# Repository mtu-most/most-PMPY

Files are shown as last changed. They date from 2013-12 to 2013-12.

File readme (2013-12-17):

MOST Push-Me-Pull-You 3D printer extruder drive

This design was developed as part of a project with the Michigan Tech Open Sustainability Technology Research Group http://www.appropedia.org/Category:MOST It is released under CC-BY-SA and was written primarily by Jerry Anzalone.

Printed Parts (count required):
motor end (1) (two different designs available) 
output_end_MkVII (1)
bearing_yoke_mk7 (1)
arm_mk7_inlet_pivot(1)
arm_mk7_inlet_spring(1)
idler_shaft (2)
input_half_4.62 (1)
output_half_4.62 (1)
Planet_4.62 (1)
Planet_4.62 (3)
carrier_MkVII_4.62 (1)

Non-printed parts (count):
M5 x 50mm hex-head cap screw (1)
M5 nut (1)
mk7 drive gear (1)
M3 x 8mm set screw (1)
M3 nut (4)
M4 x 16mm socket head cap screw (3)
M4 nylock nut (3)
M4 flat washer (9)
624zz bearing (3)
625 bearing (2)
M4 x 6mm aluminum standoff (2)
M4 nut (2)
4mm OD x 2mm ID teflon tubing of sufficient length for project
NEMA17 motor (1)
M3 x 12mm socket head cap screw (4)
M3 flat washer (8)
M3 x 45mm socket head cap screw (3)
M3 x 25mm socket head cap screw (1)
~25mm x ~10mm stiff compression spring (1)
608zz bearing (2)

Instructions
Clean up the sun gear. Press an M3 nut into the set screw nut trap and start the set screw. Do not tighten the screw into the motor shaft recess. Test fit the gear by pressing it onto the motor shaft and then removing it.
Clean up the motor end and attach to motor with M3 x 12mm screws each with an M3 washer.
Clean up the output end and press an M3 nut in the nut trap near the pointed screw boss.
Clean up the planetary carrier and press the M5 x 50mm screw through the central hole, seating the hex head in the recess provided. Press an M4 nylock nut into the nut traps.
Clean up the plantary gears, carefully removing support material and protrusions from threads, Press a 624zz bearing into each of the gears. Push a M4 x 16mm screw through the bearing and place 3 M4 flat washers on the screw below the bearing. Screw the gears onto the planteray carrier, tightening each and then loosing them up.
Work the sun gear in between the three planetary gears - insuring that the screws are very loose will facilitate this step.
With the sun gear seated in the center of the three planetary gears, tighten the planetary gear screws.
Work the planetary gears into the output half with the threaded portion of the M5 screw coming out opposite the annulus gear.
Work the input half onto the other side of the planetary gears making sure the pointed case screw boss lines up with same on the output half.
Line up the flat on the motor shaft with the set screw access port in the motor end then line up the set screw on the sun gear with the flat on the motor shaft. Press the transmission towards the motor so that the sun gear is pressed onto the motor shaft.
Apply white lithium grease to the planet gears and exposed portions of the annulus gears.
Put an M3 x 45mm screw with a washer into each of the three holes in the output end.
Place a 625 bearing on the M5 screw protruding from the planetary carrier. Feed the M5 screw through the output end and align the three M3 x 45mm case screws such that the pointed screw bosses are all lined up.
Place a washer and nut on each of the three case screws and carefully tighten the assembly.
Tighten the set screw in the sun gear through access port provided in motor case.
Clean up the arms and check that the 608zz bearings fit freely in their recesses.
Place a 608zz bearing in the recess and align its ID with the idler shaft hole in the arm. Start the idler shaft and carefully pound into place - they're tight by design.
Cut the 4mm OD x 2mm ID teflon tubing to the appropriate lengths. Cut two short (70-90mm) lengths for in-feed sides.
Prepare threads in both ends of the longer pieces of tubing (Bowden sheath). (Taper ends and screw M4 nuts onto them while a 2mm drill bit is inside the tubing to keep walls from collapsing. Work slowly and back the nut off on occasion. Thread ~12mm on one side and 6mm on the other. Ream the tubing with the 2mm drill bit. Pass a length of 1.75mm filament through the tubing to check for obstruction and clear out shavings. Ream again if friction is felt.)
Place an M4 x 6mm stand off in the recesses provided in the arms. Thread the 6mm long threaded portion into the stand offs. Ream the tubing with the 2mm drill bit again and pass a length of 1.75mm filament through the tube to check for obstructions and tight areas. Ream again if necessary.
Prepare ~5mm of thread on one end of the short (in-feed) lengths of teflon tubing.
Place an M4 nut in recess located in each arm and thread the in-feed tube into it.
Feed a length of f1.75mm filament through the in-feed tube and Bowden sheath of one of the arms. Leave it in place for next several steps.
Interlock the arms and push the M3 x 25mm screw with washer through the pivot hole. Place the screw in the hole nearest the pointed case screw boss on the output end and tighten the screw into the nut.
Put the mk7 drive gear on the M5 screw, hobbed portion up. Do not tighten the set screw.
Align the hobbed portion of the drive gear with the filament that was left in one of the arms. Once the filament is centered on the hob, tighten the set screw in the drive gear. Remove the filament.
Place the output bearing spider on top of the output end, seat the remaining 625 bearing and thread the M5 nut on the M5 screw to secure in place.
Place the compression spring between the two arms at their free ends.
Drink a beverage of your choosing and celebrate.

Notes on printing gears:
Print them singly and slowly with lots of cooling.
Print the planet gears on a raft to eliminate distortion of the teeth at the first layer.

Notes:
The transmission has a ratio of 4.62:1. With typical NEMA17 motors, sufficient torque is produced to strip the Bowden sheath from its retainers, hence the use of the M4 x 6mm stand offs in the arms.

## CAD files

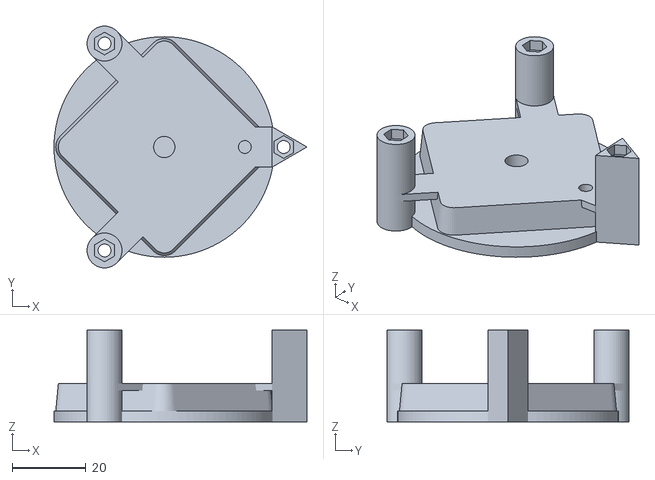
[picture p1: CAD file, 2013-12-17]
stl/output_end_MkVII.stl
68.8 x 65.8 x 25.0

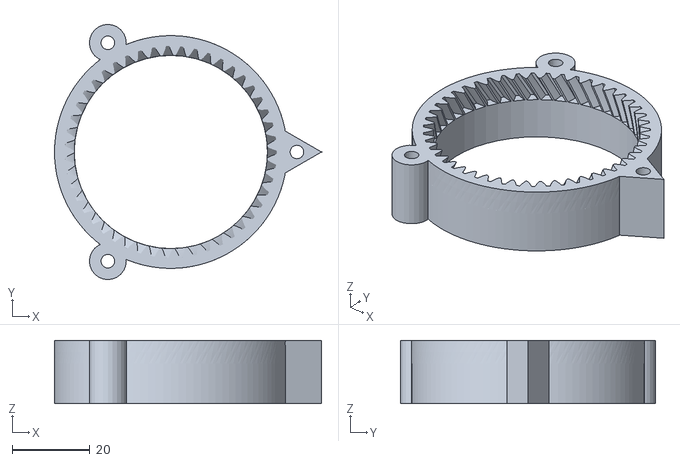
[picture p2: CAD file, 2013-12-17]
stl/output_half_4.62.stl
68.8 x 65.8 x 16.4

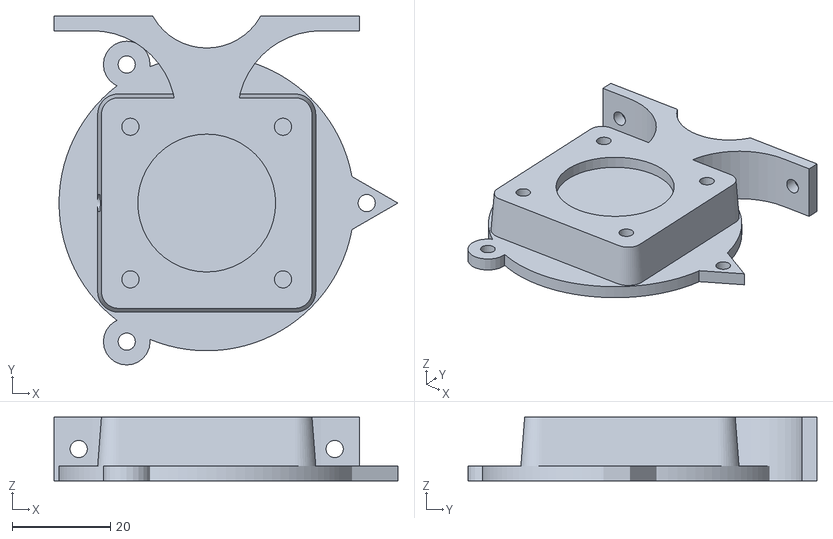
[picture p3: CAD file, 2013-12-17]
stl/motor_end_delta_mount.stl
69.8 x 70.9 x 13.0

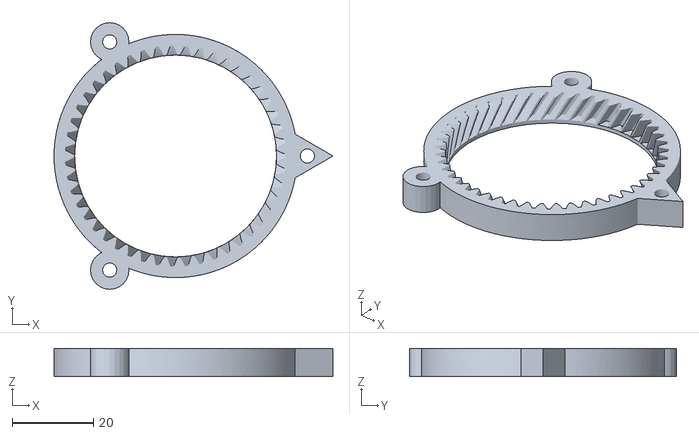
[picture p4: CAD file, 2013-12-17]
stl/input_half_4.62.stl
68.8 x 65.8 x 7.00

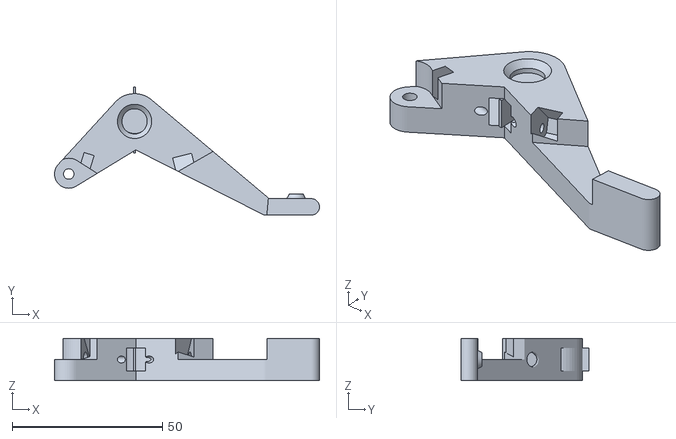
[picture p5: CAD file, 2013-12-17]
stl/arm_mk7_inlet_pivot.stl
88.3 x 42.7 x 14.0

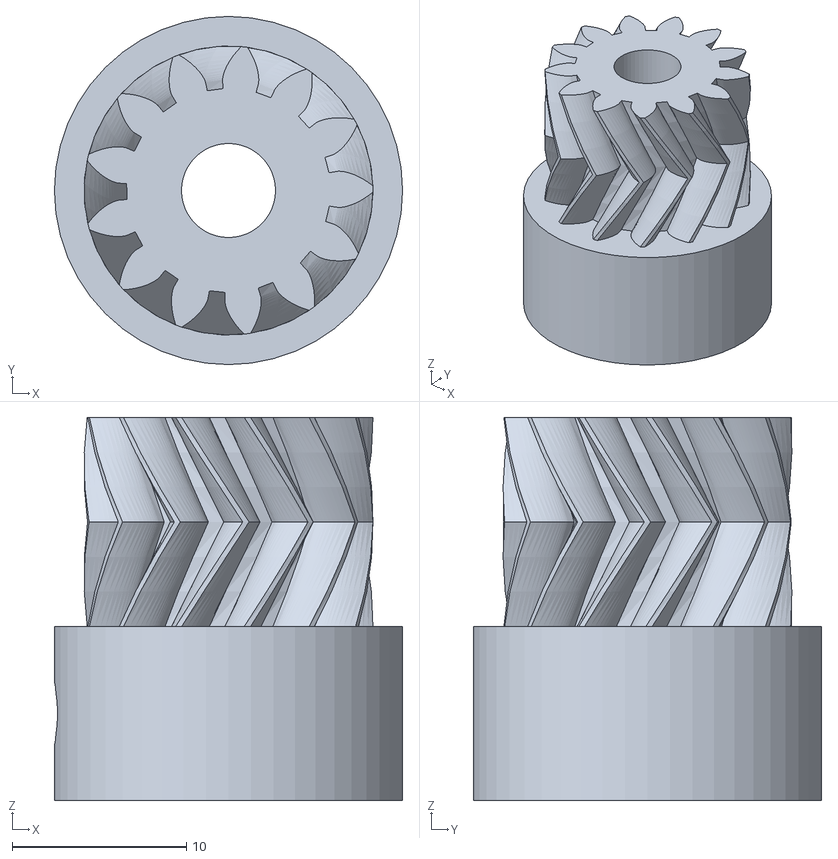
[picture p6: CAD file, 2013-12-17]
stl/sun_4.62.stl
20.0 x 20.0 x 22.0

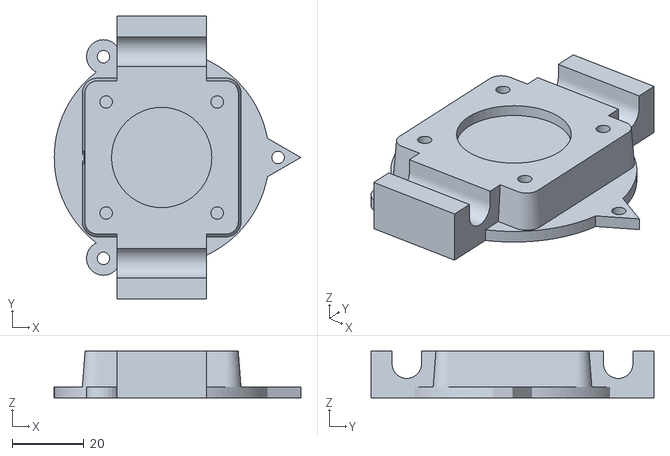
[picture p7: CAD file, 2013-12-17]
stl/motor_end_prusa_mount.stl
68.8 x 79.0 x 13.0

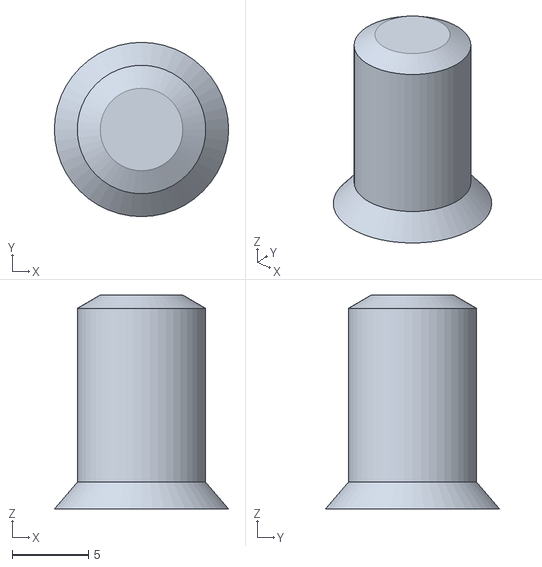
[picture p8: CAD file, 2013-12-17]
stl/idler_shaft.stl
11.4 x 11.4 x 14.0

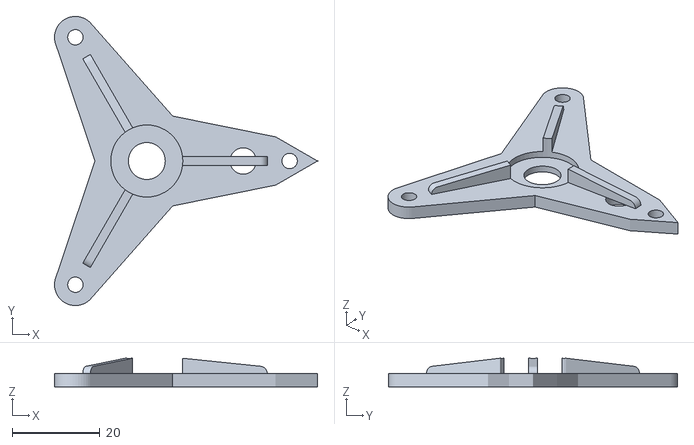
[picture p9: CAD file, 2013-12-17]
stl/bearing_yoke_mk7.stl
59.8 x 65.8 x 6.49

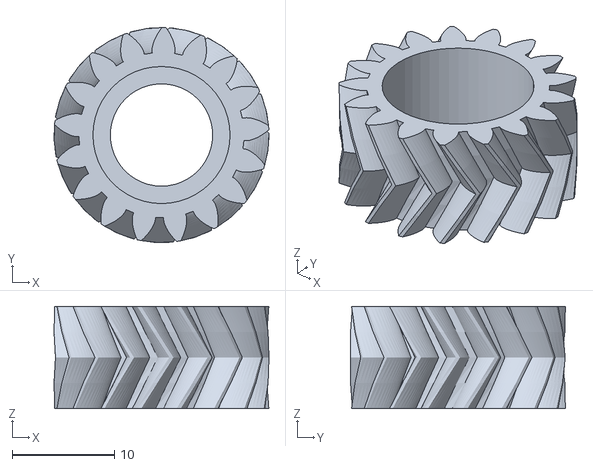
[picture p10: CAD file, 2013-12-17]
stl/Planet_4.62.stl
21.0 x 21.0 x 10.0

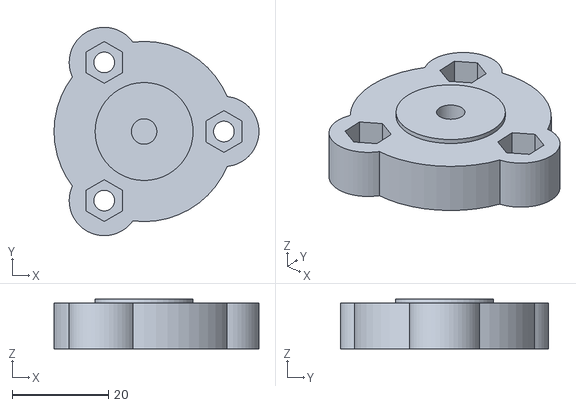
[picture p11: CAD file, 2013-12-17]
stl/carrier_MkVII_4.62.stl
42.6 x 43.3 x 10.3

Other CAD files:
stl/arm_mk7_inlet_spring.stl
